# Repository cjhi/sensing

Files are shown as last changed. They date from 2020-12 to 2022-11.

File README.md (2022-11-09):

# Sensing

Repository for all Olin Rocketry hardware and firmware.

The purpose of the avionics system is to determine when to deploy the drogue and main chutes, and to send the signal to do so to the recovery system. The flight computer contains several sensors to help detect apogee, and a microcontroller to read and process the data and send the signal.

The avionics system consists of

- a commercial-off-the-shelf (COTS) flight computer;
- a student-designed flight computer, which includes sensors, microcontroller, GPS, and radio; and
- a student-designed battery management system (BMS).

The COTS computer is a **\_** model. It has its own batteries, sensors, and radio and can trigger the recovery system independently. It is intended as a backup and is required by IREC competition rules (partly so they have a reliable altitude measurement for the competition). The BMS is described on the Power Management subteam page. It can suppy a steady 3.3V current up to about 1000 mA to the student-designed flight computer board.

**The flight computer consists of a Teensy 3.6 microcontroller and various sensors.**

- The [Teensy 3.6](https://www.pjrc.com/teensy/card9a_rev1.pdf) is computationally powerful enough for complex data processing, has many interrupt pins, and many pins in general for connecting multiple sensors. It also has a built-in SD card reader. The decision to use it was made before the Fall 2020 semester; other options were considered and may be viable for future iterations. The main drawback of the Teensy 3.6 is its cost, at around $30. This makes having multiple prototypes very expensive, especially if we want to distribute copies to team members living in separate places.
- We considered 3 different inertial measurement units (IMUs, or accelerometers):
  - [ADXL345](https://www.analog.com/media/en/technical-documentation/data-sheets/ADXL345.pdf) is a very common 3-axis accelerometer. It is widely available and was already in stock from JLC, the company manufacturing our board. This means our boards will have the ADXL345 already populated when it is shipped to us, a bonus.
  - [BMI088](https://download.mikroe.com/documents/datasheets/BMI088_Datasheet.pdf) is a 6-axis accelerometer and gyroscope (axes 4-6 are angular acceleration).
  - [BNO055](https://cdn-shop.adafruit.com/datasheets/BST_BNO055_DS000_12.pdf) is a 9-axis accelerometer, relative, and absolute gyroscope (axes 7-9 are absolute orientation).

We designed our Rev1 PCB to hold all three IMUs, so that we could test all of them at once. However, as of ordering time in January, the BMI088 and BNO055 were out of stock at Digikey and Mouser, so these were never tested.

- [MPL3115A2](https://www.nxp.com/docs/en/data-sheet/MPL3115A2.pdf) is a barometer calibrated to provide altimetry. It is the most important sensor, as it allows us to determine our absolute altitude. Our simplest apogee detection is triggered by a certain number of consecutive decreasing altitude measurements.
- Header pins for the [Adafruit Ultimate GPS Breakout (Version 3)](https://www.adafruit.com/product/746?__hstc), a $40 complete GPS module.
- Header pins for the [RFM9X LoRa Packet Radio Breakout](https://learn.adafruit.com/adafruit-rfm69hcw-and-rfm96-rfm95-rfm98-lora-packet-padio-breakouts/arduino-wiring), the currenty preferred radio (see Communications subteam page).

**Rev 1 Testing Update: Spring 2021**

The sensors on Rev1 (the ADXL345 accelerometer and the MPL3115A2 barometer) work, and the data can be read over I2C. The current data format is a csv file with time since launch, x, y, and z acceleration, pressure, altitude, and temperature. The readings from the accelerometer have very little noise when at rest (the only test performed so far - others to follow soon). The barometer has some issues. First of all, it has an offset of about 1.7 atmospheres. When those 1.7 atm are subtracted out, however, it provides high precision and sensitivity. The altitude readings are off by the same offset, as I believe they are calculated from the barometer reading anyway. The temperature has some 20 degrees F offset and significant drift of 2-5 degrees F over a few minutes. More testing to follow.

I looked at the specs and realized that the ADXL345 and MPL3115A2 together consume less than 3 mA of current at their max. Since the Teensy can output 250 mA through those pins, I don’t see why to use an external power source; we can just use the 3.3V pins on the Teensy.
The tests I have done have been using the 3.3V pin as a power source.

**Tests performed 3/26/2021:**

**Power supply test:** Get an external power supply and give 3.3V to the power inputs. Test the test points and the Teensy’s Vin pin. Test data logging onto SD card. Test sensors connected only to external power supply vs. connected to Teensy 3.3V pin vs. connected to both.

**Results:**
The transistor part of the Rev1 power management circuit did not work. For some reason, there was always only ~0.6V on both the gate and drain pins, and so 0.6V on the rest of the PCB. I tried several pin configurations and nothing helped. It worked fine when I bypassed the transistor and powered 3.3V to both the Teensy and the PCB.
The Teensy could not write to the SD card when the PCB and Teensy were powered independently; it only works when the rest of the PCB is powered through the Teensy’s dedicated 3.3V pin. Therefore, I recommend just using the Teensy’s 3.3V pin to power the sensors.

In this case, I suggest the voltage supplied by the BMS should be 3.6V instead of 3.3V, so that the linear voltage regulator on the Teensy can effectively supply the 3.3V to the sensors. Voltage regulators necessariy have a small voltage drop across them, although I came across a [source](https://forum.pjrc.com/threads/55789-Power-Teensy-3-6-with-lipo-battery?p=203568&viewfull=1#post203568) that says the Teensy will bypass its voltage regulator if the voltage is too low, so there is not necessarily an issue.

**MPL3115A2 Accuracy Test:** Take the Rev1 board up and down the stairs of the MAC building 2 times and measure altitude difference.

**Results:**
The readings are inaccurate, yet very precise. The pressure has reads on the order of 200 kPa, which is double what is expected (1 atmosphere is about 100 kPa), and the temperature reads 90 degrees F in a 70 degree room. Yet after the offset is subtracted, the sensor tracks changes in height of less than 20 feet (the distance between floors in the MAC, and the highest resolution analyzed) quite well. The graph below shows the corrected elevation and temperature over the course of my trip up and down the stairs of the MAC, then outside onto the great lawn and up to the 4th floor of West Hall. There is some drift over time as it sat on my desk after “landing,” on the order of 20 feet over 20 minutes. This is worrying, but it will likely not be a problem during a launch lasting a few minutes.

rev1 full schematic

**Developing the Rev 2 board**

With the ADXL345 and MPL3115A2 sensors confirmed to work, the main objective of the Rev 2 board is to make it fit into the avionics bay. The final board is 80mm tall by 72mm wide and has a mounting hole in each corner. The power supply transistor circuit has been replaced with a power multiplexer, a zener diode was added for overvoltage protection, and the power from the BMS goes directly into the Vin pin on the Teensy; the sensors and other circuitry are powered by the Teensy's 3.3V pin as discussed above. Additionally, 5 debugging LEDs, one power LED, and a [buzzer](https://www.digikey.com/en/products/detail/mallory-sonalert-products-inc/PT-1340P-P10-PQ/4996070) have also been added and are controlled by spare digital pins on the Teensy. A 10uF capacitor was added between the power and ground pins of the radio upon testing by the Communications team.

The board has been ordered from JLC and will arrive within a couple days.

## Guide to creating PCBs

**The process for creating the flight computer PCB has multiple stages:**
  1. Components are selected, including the microcontroller and sensors.
  2. Schematics are created for each sensor individually. This mainly involves copying the circuit diagram from the datasheets for each sensor. Every sensor needs at least two capacitors for its power source, and some require external pull-up resistors, for example. The BNO055 is connected to an external crystal oscillator. It’s also a good idea to add test points (basically large, labelled vias) for debugging purposes. We tried to add a test point to every trace on the schematic that would not be directly connected to the microcontroller (because we can access those traces directly through the microcontroller’s pins). 
  3. For the Rev1 board, footprints for the BNO055 and MPL3115A2 were created by copying the dimensions given by the datasheets. The other footprints were downloaded from snapeda.com. In reality, the only reason to create them manually is to get practice with KiCAD, which is why it was done this way for two of the sensors; in future, snapeda.com likely has all the footprints we will need, without the possibility of human error.*
  4. At this stage, layouts are also created for the supporting circuitry surrounding each sensor individually. These layouts will be manually recreated later, but it is easier to go through a few iterations to find the optimal footprint placements now, before all the layouts are combined on one board.
  5. Now, all of the individual schematics are moved into one place. This can be done in the KiCAD schematic editor (eeschema) by clicking File -> Append Schematic Sheet Content -> then navigate to the schematic to import and click Use Relative Path.
  6. Now all the schematics can be hooked up together; in this case it means connecting each sensor’s communication pins to the Teensy and power and ground to the power supply. A small circuit for regulating the power supply from the BMS, as well as header pins for the BMS and GPS and radio breakout boards are also added to this schematic.
  7. Review the schematics with the flight computer sub-team. Hopefully we have been checking in all along, but now is the last chance to make changes before a lot of work goes into the layout. After this, even small changes to the schematic can be very hard to implement in the layout without starting over.
  8. The layout of all the components for the final PCB is created. You cannot copy and paste the layouts created earlier for individual sensors, but you can follow the prior layouts as a guide. For the Rev1 board, we kept the components in the same relative orientation but did not pack them as closely together, to make debugging and potential fixes easier. During the layout process, it will probably make sense to swap the order of some pins connected to the microcontroller, in order to untangle the traces, or reduce the number of times traces have to cross over. Most pins on the Teensy 3.6 can function in the same way, so switching which pins are connected to which sensor is not a problem. Be careful not to switch the order of SCK and SDA; MISO and MOSI; or RX and TX; these pins are not interchangeable.
  9. It's a good idea to add filled zones on the front and back of the board. Having filled zones helps reduce signal noise and is standard practice. It also means there are fewer traces you have to draw. I usually make my filled zones be ground on both sides of the PCB, with an abundance of vias throughout the board to connect the front and back ground planes. Remember to press 'B' to redraw the zones in KiCAD.
  10. When the layout is done and reviewed, it is sent to JLC, our manufacturer. JLC can populate the PCB with basic components like capacitors, resistors, and even the ADXL345. They did not have any of the other sensors in stock, so we will solder those on campus. We will also solder header pins and large components like the power-regulating MOSFET transistor (which will be discontinued in Rev2).
  11. Next up is writing the firmware to test the sensors and hopefully getting some data!

\* In fact, I did make a very significant error while copying the footprint from the datasheet for both the BNO055 and the MPL3115. I copied the pads as they were shown in the datasheet, which was a bottom-up view. What matters for the layout is the top-down view (think about how the sensor sits on the PCB; you want to design the pads so they sit directly beneath the sensor). When you design the pads using the bottom-up view, you get a mirror image of how they are supposed to be. Moreover, since the footprints are often symmetrical, it can be impossible to tell you’ve made a mistake, until you realize that the pins things are supposed to be connected to are actually on the opposite side of the chip.

### Rev2 images

**Rev2 full schematic**

rev2 full schematic

**Rev2 power supply**

rev1 power supply

**Rev2 layout**

rev1 layout

**Rev2 3D model (front)**

rev1 3D model front

**Rev2 3D model (back)**

rev1 3D model back

### Rev1 images

**Rev1 full schematic**

rev1 full schematic

**Rev1 power supply**

rev1 power supply

**Rev1 layout**

rev1 layout

**Rev1 3D model (front)**

rev1 3D model front

**Rev1 3D model (back)**

rev1 3D model back

## Ordering PCBs From JLCPCB

For ordering the boards, go to JLCPCB.com (https://jlcpcb.com/RAT), and click on "Quote Now" button.

jlcpcb quote

JLCPCB (ShenzhenJLC Electronics Co., Ltd.), is the largest PCB prototype enterprise in China, and a high-tech manufacturer specializing in quick PCB prototype and small-batch PCB production. You can order a minimum of 5 PCBs for just $2.

First: Upload the gerber files for the board by clicking the "Add gerber file" button. You’ll notice a message at the bottom if the file is successfully uploaded.

jlcpbc gerber

A correctly uploaded gerber folder renders the board as follows:

jlcpcb render

Second: In order to get the board assembled (optional, based on the project requirements), select the "SMT Assembly option. It is important to select the side of the PCB that needs to be assembled, as well as the quantity for SMT. Press the "Confirm" button, then press the "Next" button.

jlcpcb smt

Third: upload the BOM (Bill of Material) and CPL (Component Placement List) files and click the "Next" button. It is necessary to make sure that each of these files follow the jlcpcb specified BOM and CPL formats, respectively:

- [Sample BOM](https://jlcpcb.com//video/JLCSMT_Sample_BOM1.xlsx?_ga=2.42560357.1905056644.1612161700-100444678.1610257845)
- [Sample CPL](https://jlcpcb.com//video/JLCSMT_Sample_CPL1.xlsx?_ga=2.42560357.1905056644.1612161700-100444678.1610257845)
- [SMT FAQ's](https://support.jlcpcb.com/category/78-smt-assembly?_ga=2.42560357.1905056644.1612161700-100444678.1610257845)

Note: If there is an issue with the BOM/CPL formatting, the the page will keep erroring out until it is resolved.

jlcpcb bom

Fourth: The parts are automatically detected through the uploaded BOM. They are also matched against jlcpcb's in-stock parts. It is important to go through each row and confirm if the auto-detected parts are the desired parts. Some parts will remain undetected if they cannot be assembled through SMT and require manual assembly post-deilvery.

jlcpcb parts

Fifth: The website renders an assembled board using the CPL file. This feature can be used to review the placement of the components (including orientation). Once carefull reviewed, the next step is to download a list of parts remaining to be assembled towards the bottom of this page view. It is important to place an order for the remaining components to be manually assembled upon delivery.

jlcpcb review

Sixth: Click on the “Save to Cart” button. Then, click on the "Secure Checkout" button.

jlcpcb checkout

Last: Add the payment details and choose the suitable delivery method (this includes FedEx, DHL, and standard mail options). Then, place the order.

Optional: To review the production status of the board, click on the "Order History" button under username. Then, click on In Production > view progress to obtain timestamps for each of the production steps in real time.

jlcpcb production

jlcpcb production progress

**Design Reviews**

-November 11, 2022 6:00 PM

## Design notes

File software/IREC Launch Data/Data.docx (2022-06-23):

0

RSSI: -102

Got: Time: 14091326 Phase: 2 Arm: 1299.062500 Main: 1741.262451 Alt: 1284.187500

RSSI: -102

Got: Time: 140914500

RSSI: -102

Got: Time: 14091326 Phase: 2 Arm: 1299.062500 Main: 1741.262451 Alt: 1284.187500

RSSI: -102

Got: Time: 140914500

RSSI: -102

Got: Time: 14091326 Phase: 2 Arm: 1299.062500 Main: 1741.262451 Alt: 1284.187500

RSSI: -102

Got: Time: 140914Arduino LoRa RX Test!

LoRa radio init OK!

Set Freq to: 915.00

Got: Time: 14093661 Phase: 2 Arm: 1299.062500 Main: 1741.262451 Alt: 1284.312500

RSSI: -103

Got: Time: 14093828 Phase: 2 Arm: 1299.062500 Main: 1741.262451 Alt: 1284.312500

RSSI: -102

Got: Time: 14093994 Phase: 2 Arm: 1299.062500 Main: 1741.262451 Alt: 1284.250000

RSSI: -102

Got: Time: 14094161 Phase: 2 Arm: 1299.062500 Main: 1741.262451 Alt: 1284.125000

RSSI: -102

Got: Time: 14094328 Phase: 2 Arm: 1299.062500 Main: 1741.262451 Alt: 1283.437500

RSSI: -101

Got: Time: 14094495 Phase: 2 Arm: 1299.062500 Main: 1741.262451 Alt: 1284.625000

RSSI: -102

Got: Time: 14094661 Phase: 2 Arm: 1299.062500 Main: 1741.262451 Alt: 1284.312500

RSSI: -103

Got: Time: 14094828 Phase: 2 Arm: 1299.062500 Main: 1741.262451 Alt: 1284.312500

RSSI: -103

Got: Time: 14094995 Phase: 2 Arm: 1299.062500 Main: 1741.262451 Alt: 1284.375000

RSSI: -102

Got: Time: 14095162 Phase: 2 Arm: 1299.062500 Main: 1741.262451 Alt: 1283.937500

RSSI: -99

Got: Time: 14095329 Phase: 2 Arm: 1299.062500 Main: 1741.262451 Alt: 1284.187500

RSSI: -103

Got: Time: 14095495 Phase: 2 Arm: 1299.062500 Main: 1741.262451 Alt: 1284.187500

RSSI: -103

Got: Time: 14095662 Phase: 2 Arm: 1299.062500 Main: 1741.262451 Alt: 1284.437500

RSSI: -103

Got: Time: 14095829 Phase: 2 Arm: 1299.062500 Main: 1741.262451 Alt: 1283.875000

RSSI: -103

Got: Time: 14095996 Phase: 2 Arm: 1299.062500 Main: 1741.262451 Alt: 1284.375000

RSSI: -102

Got: Time: 14096162 Phase: 2 Arm: 1299.062500 Main: 1741.262451 Alt: 1283.937500

RSSI: -101

Got: Time: 14096329 Phase: 2 Arm: 1299.062500 Main: 1741.262451 Alt: 1284.187500

RSSI: -102

Got: Time: 14096496 Phase: 2 Arm: 1299.062500 Main: 1741.262451 Alt: 1283.937500

RSSI: -102

Got: Time: 14096663 Phase: 2 Arm: 1299.062500 Main: 1741.262451 Alt: 1284.000000

RSSI: -103

Got: Time: 14096829 Phase: 2 Arm: 1299.062500 Main: 1741.262451 Alt: 1284.125000

RSSI: -102

Got: Time: 14096996 Phase: 2 Arm: 1299.062500 Main: 1741.262451 Alt: 1284.312500

RSSI: -103

Got: Time: 14097163 Phase: 2 Arm: 1299.062500 Main: 1741.262451 Alt: 1283.812500

RSSI: -99

Got: Time: 14097330 Phase: 2 Arm: 1299.062500 Main: 1741.262451 Alt: 1284.375000

RSSI: -102

Got: Time: 14097497 Phase: 2 Arm: 1299.062500 Main: 1741.262451 Alt: 1283.562500

RSSI: -102

Got: Time: 14097663 Phase: 2 Arm: 1299.062500 Main: 1741.262451 Alt: 1283.937500

RSSI: -103

Got: Time: 14097830 Phase: 2 Arm: 1299.062500 Main: 1741.262451 Alt: 1284.375000

RSSI: -103

Got: Time: 14097997 Phase: 2 Arm: 1299.062500 Main: 1741.262451 Alt: 1284.125000

RSSI: -103

Got: Time: 14098164 Phase: 2 Arm: 1299.062500 Main: 1741.262451 Alt: 1284.312500

RSSI: -98

Got: Time: 14098330 Phase: 2 Arm: 1299.062500 Main: 1741.262451 Alt: 1284.187500

RSSI: -103

Got: Time: 14098497 Phase: 2 Arm: 1299.062500 Main: 1741.262451 Alt: 1284.187500

RSSI: -102

Got: Time: 14098664 Phase: 2 Arm: 1299.062500 Main: 1741.262451 Alt: 1283.937500

RSSI: -103

Got: Time: 14098831 Phase: 2 Arm: 1299.062500 Main: 1741.262451 Alt: 1283.875000

RSSI: -102

Got: Time: 14098997 Phase: 2 Arm: 1299.062500 Main: 1741.262451 Alt: 1283.937500

RSSI: -103

Got: Time: 14099164 Phase: 2 Arm: 1299.062500 Main: 1741.262451 Alt: 1283.312500

RSSI: -100

Got: Time: 14099331 Phase: 2 Arm: 1299.062500 Main: 1741.262451 Alt: 1283.312500

RSSI: -99

Got: Time: 14099498 Phase: 2 Arm: 1299.062500 Main: 1741.262451 Alt: 1283.750000

RSSI: -102

Got: Time: 14099665 Phase: 2 Arm: 1299.062500 Main: 1741.262451 Alt: 1283.562500

RSSI: -102

Got: Time: 14099831 Phase: 2 Arm: 1299.062500 Main: 1741.262451 Alt: 1284.187500

RSSI: -102

Got: Time: 14099998 Phase: 2 Arm: 1299.062500 Main: 1741.262451 Alt: 1283.937500

RSSI: -102

Got: Time: 14100165 Phase: 2 Arm: 1299.062500 Main: 1741.262451 Alt: 1284.000000

RSSI: -102

Got: Time: 14100332 Phase: 2 Arm: 1299.062500 Main: 1741.262451 Alt: 1284.062500

RSSI: -103

Got: Time: 14100498 Phase: 2 Arm: 1299.062500 Main: 1741.262451 Alt: 1284.062500

RSSI: -102

Got: Time: 14100665 Phase: 2 Arm: 1299.062500 Main: 1741.262451 Alt: 1283.937500

RSSI: -103

Got: Time: 14100832 Phase: 2 Arm: 1299.062500 Main: 1741.262451 Alt: 1283.875000

RSSI: -103

Got: Time: 14100999 Phase: 2 Arm: 1299.062500 Main: 1741.262451 Alt: 1283.937500

RSSI: -103

Got: Time: 14101165 Phase: 2 Arm: 1299.062500 Main: 1741.262451 Alt: 1284.375000

RSSI: -101

Got: Time: 14101332 Phase: 2 Arm: 1299.062500 Main: 1741.262451 Alt: 1284.000000

RSSI: -103

Got: Time: 14101499 Phase: 2 Arm: 1299.062500 Main: 1741.262451 Alt: 1284.187500

RSSI: -102

Got: Time: 14101666 Phase: 2 Arm: 1299.062500 Main: 1741.262451 Alt: 1284.062500

RSSI: -102

Got: Time: 14101832 Phase: 2 Arm: 1299.062500 Main: 1741.262451 Alt: 1284.000000

RSSI: -102

Got: Time: 14101999 Phase: 2 Arm: 1299.062500 Main: 1741.262451 Alt: 1284.562500

RSSI: -103

Got: Time: 14102166 Phase: 2 Arm: 1299.062500 Main: 1741.262451 Alt: 1283.937500

RSSI: -99

Got: Time: 14102333 Phase: 2 Arm: 1299.062500 Main: 1741.262451 Alt: 1283.562500

RSSI: -102

Got: Time: 14102500 Phase: 2 Arm: 1299.062500 Main: 1741.262451 Alt: 1283.750000

RSSI: -102

Got: Time: 14102666 Phase: 2 Arm: 1299.062500 Main: 1741.262451 Alt: 1284.062500

RSSI: -102

Got: Time: 14102833 Phase: 2 Arm: 1299.062500 Main: 1741.262451 Alt: 1284.375000

RSSI: -102

Got: Time: 14103000 Phase: 2 Arm: 1299.062500 Main: 1741.262451 Alt: 1283.937500

RSSI: -102

Got: Time: 14103167 Phase: 2 Arm: 1299.062500 Main: 1741.262451 Alt: 1284.375000

RSSI: -100

Got: Time: 14103333 Phase: 2 Arm: 1299.062500 Main: 1741.262451 Alt: 1283.625000

RSSI: -102

Got: Time: 14103500 Phase: 2 Arm: 1299.062500 Main: 1741.262451 Alt: 1283.375000

RSSI: -102

Got: Time: 14103667 Phase: 2 Arm: 1299.062500 Main: 1741.262451 Alt: 1283.750000

RSSI: -102

Got: Time: 14103834 Phase: 2 Arm: 1299.062500 Main: 1741.262451 Alt: 1284.375000

RSSI: -102

Got: Time: 14104000 Phase: 2 Arm: 1299.062500 Main: 1741.262451 Alt: 1283.562500

RSSI: -102

Got: Time: 14104167 Phase: 2 Arm: 1299.062500 Main: 1741.262451 Alt: 1283.875000

RSSI: -100

Got: Time: 14104334 Phase: 2 Arm: 1299.062500 Main: 1741.262451 Alt: 1284.250000

RSSI: -100

Got: Time: 14104501 Phase: 2 Arm: 1299.062500 Main: 1741.262451 Alt: 1284.187500

RSSI: -102

Got: Time: 14104668 Phase: 2 Arm: 1299.062500 Main: 1741.262451 Alt: 1284.187500

RSSI: -103

Got: Time: 14104834 Phase: 2 Arm: 1299.062500 Main: 1741.262451 Alt: 1284.562500

RSSI: -102

Got: Time: 14105001 Phase: 2 Arm: 1299.062500 Main: 1741.262451 Alt: 1283.812500

RSSI: -102

Got: Time: 14105168 Phase: 2 Arm: 1299.062500 Main: 1741.262451 Alt: 1284.375000

RSSI: -96

Got: Time: 14105335 Phase: 2 Arm: 1299.062500 Main: 1741.262451 Alt: 1283.937500

RSSI: -102

Got: Time: 14105501 Phase: 2 Arm: 1299.062500 Main: 1741.262451 Alt: 1284.312500

RSSI: -102

Got: Time: 14105668 Phase: 2 Arm: 1299.062500 Main: 1741.262451 Alt: 1283.937500

RSSI: -102

Got: Time: 14105835 Phase: 2 Arm: 1299.062500 Main: 1741.262451 Alt: 1284.000000

RSSI: -102

Got: Time: 14106002 Phase: 2 Arm: 1299.062500 Main: 1741.262451 Alt: 1284.562500

RSSI: -102

Got: Time: 14106168 Phase: 2 Arm: 1299.062500 Main: 1741.262451 Alt: 1283.687500

RSSI: -98

Got: Time: 14106335 Phase: 2 Arm: 1299.062500 Main: 1741.262451 Alt: 1284.187500

RSSI: -102

Got: Time: 14106502 Phase: 2 Arm: 1299.062500 Main: 1741.262451 Alt: 1283.750000

RSSI: -102

Got: Time: 14106669 Phase: 2 Arm: 1299.062500 Main: 1741.262451 Alt: 1283.937500

RSSI: -103

Got: Time: 14106836 Phase: 2 Arm: 1299.062500 Main: 1741.262451 Alt: 1284.375000

RSSI: -103

Got: Time: 14107002 Phase: 2 Arm: 1299.062500 Main: 1741.262451 Alt: 1283.937500

RSSI: -102

Got: Time: 14107169 Phase: 2 Arm: 1299.062500 Main: 1741.262451 Alt: 1283.750000

RSSI: -97

Got: Time: 14107336 Phase: 2 Arm: 1299.062500 Main: 1741.262451 Alt: 1284.062500

RSSI: -102

Got: Time: 14107503 Phase: 2 Arm: 1299.062500 Main: 1741.262451 Alt: 1284.375000

RSSI: -102

Got: Time: 14107669 Phase: 2 Arm: 1299.062500 Main: 1741.262451 Alt: 1283.562500

RSSI: -102

Got: Time: 14107836 Phase: 2 Arm: 1299.062500 Main: 1741.262451 Alt: 1284.250000

RSSI: -103

Got: Time: 14108170 Phase: 2 Arm: 1299.062500 Main: 1741.262451 Alt: 1283.937500

RSSI: -101

Got: Time: 14108336 Phase: 2 Arm: 1299.062500 Main: 1741.262451 Alt: 1283.937500

RSSI: -102

Got: Time: 14108503 Phase: 2 Arm: 1299.062500 Main: 1741.262451 Alt: 1284.500000

RSSI: -102

Got: Time: 14108670 Phase: 2 Arm: 1299.062500 Main: 1741.262451 Alt: 1283.687500

RSSI: -102

Got: Time: 14108837 Phase: 2 Arm: 1299.062500 Main: 1741.262451 Alt: 1284.125000

RSSI: -102

Got: Time: 14109004 Phase: 2 Arm: 1299.062500 Main: 1741.262451 Alt: 1284.000000

RSSI: -102

Got: Time: 14109170 Phase: 2 Arm: 1299.062500 Main: 1741.262451 Alt: 1283.937500

RSSI: -101

Got: Time: 14109337 Phase: 2 Arm: 1299.062500 Main: 1741.262451 Alt: 1284.500000

RSSI: -102

Got: Time: 14109504 Phase: 2 Arm: 1299.062500 Main: 1741.262451 Alt: 1284.187500

RSSI: -102

Got: Time: 14109671 Phase: 2 Arm: 1299.062500 Main: 1741.262451 Alt: 1284.562500

RSSI: -102

Got: Time: 14109837 Phase: 2 Arm: 1299.062500 Main: 1741.262451 Alt: 1284.125000

RSSI: -102

Got: Time: 14110004 Phase: 2 Arm: 1299.062500 Main: 1741.262451 Alt: 1284.375000

RSSI: -103

Got: Time: 14110171 Phase: 2 Arm: 1299.062500 Main: 1741.262451 Alt: 1284.500000

RSSI: -101

Got: Time: 14110338 Phase: 2 Arm: 1299.062500 Main: 1741.262451 Alt: 1284.312500

RSSI: -102

Got: Time: 14110504 Phase: 2 Arm: 1299.062500 Main: 1741.262451 Alt: 1284.187500

RSSI: -102

Got: Time: 14110671 Phase: 2 Arm: 1299.062500 Main: 1741.262451 Alt: 1283.750000

RSSI: -102

Got: Time: 14110838 Phase: 2 Arm: 1299.062500 Main: 1741.262451 Alt: 1283.687500

RSSI: -102

Got: Time: 14111005 Phase: 2 Arm: 1299.062500 Main: 1741.262451 Alt: 1283.562500

RSSI: -102

Got: Time: 14111172 Phase: 2 Arm: 1299.062500 Main: 1741.262451 Alt: 1283.750000

RSSI: -102

Got: Time: 14111338 Phase: 2 Arm: 1299.062500 Main: 1741.262451 Alt: 1284.687500

RSSI: -102

Got: Time: 14111505 Phase: 2 Arm: 1299.062500 Main: 1741.262451 Alt: 1283.750000

RSSI: -102

Got: Time: 14111672 Phase: 2 Arm: 1299.062500 Main: 1741.262451 Alt: 1284.062500

RSSI: -102

Got: Time: 14111839 Phase: 2 Arm: 1299.062500 Main: 1741.262451 Alt: 1283.812500

RSSI: -102

Got: Time: 14112005 Phase: 2 Arm: 1299.062500 Main: 1741.262451 Alt: 1284.187500

RSSI: -102

Got: Time: 14112172 Phase: 2 Arm: 1299.062500 Main: 1741.262451 Alt: 1284.750000

RSSI: -101

Got: Time: 14112339 Phase: 2 Arm: 1299.062500 Main: 1741.262451 Alt: 1284.187500

RSSI: -102

Got: Time: 14112506 Phase: 2 Arm: 1299.062500 Main: 1741.262451 Alt: 1284.187500

RSSI: -102

Got: Time: 14112672 Phase: 2 Arm: 1299.062500 Main: 1741.262451 Alt: 1283.750000

RSSI: -102

Got: Time: 14112839 Phase: 2 Arm: 1299.062500 Main: 1741.262451 Alt: 1284.187500

RSSI: -102

Got: Time: 14113006 Phase: 2 Arm: 1299.062500 Main: 1741.262451 Alt: 1284.562500

RSSI: -102

Got: Time: 14113173 Phase: 2 Arm: 1299.062500 Main: 1741.262451 Alt: 1284.125000

RSSI: -100

Got: Time: 14113339 Phase: 2 Arm: 1299.062500 Main: 1741.262451 Alt: 1283.937500

RSSI: -102

Got: Time: 14113506 Phase: 2 Arm: 1299.062500 Main: 1741.262451 Alt: 1283.937500

RSSI: -102

Got: Time: 14113673 Phase: 2 Arm: 1299.062500 Main: 1741.262451 Alt: 1283.750000

RSSI: -102

Got: Time: 14113840 Phase: 2 Arm: 1299.062500 Main: 1741.262451 Alt: 1284.187500

RSSI: -102

Got: Time: 14114007 Phase: 2 Arm: 1299.062500 Main: 1741.262451 Alt: 1283.250000

RSSI: -102

Got: Time: 14114173 Phase: 2 Arm: 1299.062500 Main: 1741.262451 Alt: 1284.562500

RSSI: -101

Got: Time: 14114340 Phase: 2 Arm: 1299.062500 Main: 1741.262451 Alt: 1284.437500

RSSI: -101

Got: Time: 14114507 Phase: 2 Arm: 1299.062500 Main: 1741.262451 Alt: 1283.750000

RSSI: -102

Got: Time: 14114674 Phase: 2 Arm: 1299.062500 Main: 1741.262451 Alt: 1284.750000

RSSI: -102

Got: Time: 14114840 Phase: 2 Arm: 1299.062500 Main: 1741.262451 Alt: 1284.250000

RSSI: -102

Got: Time: 14115007 Phase: 2 Arm: 1299.062500 Main: 1741.262451 Alt: 1284.250000

RSSI: -102

Got: Time: 14115174 Phase: 2 Arm: 1299.062500 Main: 1741.262451 Alt: 1283.687500

RSSI: -98

Got: Time: 14115341 Phase: 2 Arm: 1299.062500 Main: 1741.262451 Alt: 1284.062500

RSSI: -102

Got: Time: 14115507 Phase: 2 Arm: 1299.062500 Main: 1741.262451 Alt: 1284.375000

RSSI: -102

Got: Time: 14115674 Phase: 2 Arm: 1299.062500 Main: 1741.262451 Alt: 1284.187500

RSSI: -102

Got: Time: 14115841 Phase: 2 Arm: 1299.062500 Main: 1741.262451 Alt: 1284.687500

RSSI: -102

Got: Time: 14116008 Phase: 2 Arm: 1299.062500 Main: 1741.262451 Alt: 1284.375000

RSSI: -102

Got: Time: 14116175 Phase: 2 Arm: 1299.062500 Main: 1741.262451 Alt: 1284.187500

RSSI: -97

Got: Time: 14116341 Phase: 2 Arm: 1299.062500 Main: 1741.262451 Alt: 1284.000000

RSSI: -102

Got: Time: 14116508 Phase: 2 Arm: 1299.062500 Main: 1741.262451 Alt: 1284.812500

RSSI: -102

Got: Time: 14116675 Phase: 2 Arm: 1299.062500 Main: 1741.262451 Alt: 1284.250000

RSSI: -102

Got: Time: 14116842 Phase: 2 Arm: 1299.062500 Main: 1741.262451 Alt: 1284.500000

RSSI: -103

Got: Time: 14117008 Phase: 2 Arm: 1299.062500 Main: 1741.262451 Alt: 1284.375000

RSSI: -102

Got: Time: 14117175 Phase: 2 Arm: 1299.062500 Main: 1741.262451 Alt: 1283.937500

RSSI: -98

Got: Time: 14117342 Phase: 2 Arm: 1299.062500 Main: 1741.262451 Alt: 1283.812500

RSSI: -102

Got: Time: 14117509 Phase: 2 Arm: 1299.062500 Main: 1741.262451 Alt: 1284.125000

RSSI: -102

Got: Time: 14117675 Phase: 2 Arm: 1299.062500 Main: 1741.262451 Alt: 1284.187500

RSSI: -102

Got: Time: 14117842 Phase: 2 Arm: 1299.062500 Main: 1741.262451 Alt: 1284.375000

RSSI: -102

Got: Time: 14118009 Phase: 2 Arm: 1299.062500 Main: 1741.262451 Alt: 1284.000000

RSSI: -102

Got: Time: 14118176 Phase: 2 Arm: 1299.062500 Main: 1741.262451 Alt: 1283.937500

RSSI: -97

Got: Time: 14118343 Phase: 2 Arm: 1299.062500 Main: 1741.262451 Alt: 1283.750000

RSSI: -102

Got: Time: 14118509 Phase: 2 Arm: 1299.062500 Main: 1741.262451 Alt: 1283.750000

RSSI: -102

Got: Time: 14118676 Phase: 2 Arm: 1299.062500 Main: 1741.262451 Alt: 1284.562500

RSSI: -102

Got: Time: 14118843 Phase: 2 Arm: 1299.062500 Main: 1741.262451 Alt: 1284.125000

RSSI: -102

Got: Time: 14119010 Phase: 2 Arm: 1299.062500 Main: 1741.262451 Alt: 1284.437500

RSSI: -102

Got: Time: 14119176 Phase: 2 Arm: 1299.062500 Main: 1741.262451 Alt: 1284.312500

RSSI: -98

Got: Time: 14119343 Phase: 2 Arm: 1299.062500 Main: 1741.262451 Alt: 1283.937500

RSSI: -100

Got: Time: 14119510 Phase: 2 Arm: 1299.062500 Main: 1741.262451 Alt: 1283.687500

RSSI: -103

Got: Time: 14119677 Phase: 2 Arm: 1299.062500 Main: 1741.262451 Alt: 1284.187500

RSSI: -103

Got: Time: 14119843 Phase: 2 Arm: 1299.062500 Main: 1741.262451 Alt: 1284.375000

RSSI: -103

Got: Time: 14120177 Phase: 2 Arm: 1299.062500 Main: 1741.262451 Alt: 1284.312500

RSSI: -99

Got: Time: 14120344 Phase: 2 Arm: 1299.062500 Main: 1741.262451 Alt: 1284.562500

RSSI: -103

Got: Time: 14120510 Phase: 2 Arm: 1299.062500 Main: 1741.262451 Alt: 1284.937500

RSSI: -103

Got: Time: 14120677 Phase: 2 Arm: 1299.062500 Main: 1741.262451 Alt: 1284.312500

RSSI: -103

Got: Time: 14120844 Phase: 2 Arm: 1299.062500 Main: 1741.262451 Alt: 1284.562500

RSSI: -103

Got: Time: 14121011 Phase: 2 Arm: 1299.062500 Main: 1741.262451 Alt: 1284.437500

RSSI: -102

Got: Time: 14121178 Phase: 2 Arm: 1299.062500 Main: 1741.262451 Alt: 1284.687500

RSSI: -99

Got: Time: 14121344 Phase: 2 Arm: 1299.062500 Main: 1741.262451 Alt: 1284.562500

RSSI: -103

Got: Time: 14121511 Phase: 2 Arm: 1299.062500 Main: 1741.262451 Alt: 1284.375000

RSSI: -103

Got: Time: 14121678 Phase: 2 Arm: 1299.062500 Main: 1741.262451 Alt: 1284.375000

RSSI: -103

Got: Time: 14121845 Phase: 2 Arm: 1299.062500 Main: 1741.262451 Alt: 1283.937500

RSSI: -102

Got: Time: 14122011 Phase: 2 Arm: 1299.062500 Main: 1741.262451 Alt: 1284.375000

RSSI: -103

Got: Time: 14122178 Phase: 2 Arm: 1299.062500 Main: 1741.262451 Alt: 1284.125000

RSSI: -100

Got: Time: 14122345 Phase: 2 Arm: 1299.062500 Main: 1741.262451 Alt: 1283.875000

RSSI: -103

Got: Time: 14122512 Phase: 2 Arm: 1299.062500 Main: 1741.262451 Alt: 1284.375000

RSSI: -103

Got: Time: 14122678 Phase: 2 Arm: 1299.062500 Main: 1741.262451 Alt: 1284.000000

RSSI: -102

Got: Time: 14122845 Phase: 2 Arm: 1299.062500 Main: 1741.262451 Alt: 1283.812500

RSSI: -103

Got: Time: 14123012 Phase: 2 Arm: 1299.062500 Main: 1741.262451 Alt: 1284.250000

RSSI: -103

Got: Time: 14123179 Phase: 2 Arm: 1299.062500 Main: 1741.262451 Alt: 1284.062500

RSSI: -99

Got: Time: 14123346 Phase: 2 Arm: 1299.062500 Main: 1741.262451 Alt: 1283.875000

RSSI: -102

Got: Time: 14123512 Phase: 2 Arm: 1299.062500 Main: 1741.262451 Alt: 1283.937500

RSSI: -103

Got: Time: 14123679 Phase: 2 Arm: 1299.062500 Main: 1741.262451 Alt: 1283.625000

RSSI: -102

Got: Time: 14123846 Phase: 2 Arm: 1299.062500 Main: 1741.262451 Alt: 1284.187500

RSSI: -103

Got: Time: 14124013 Phase: 2 Arm: 1299.062500 Main: 1741.262451 Alt: 1284.562500

RSSI: -102

Got: Time: 14124179 Phase: 2 Arm: 1299.062500 Main: 1741.262451 Alt: 1284.187500

RSSI: -100

Got: Time: 14124346 Phase: 2 Arm: 1299.062500 Main: 1741.262451 Alt: 1283.937500

RSSI: -99

Got: Time: 14124513 Phase: 2 Arm: 1299.062500 Main: 1741.262451 Alt: 1284.375000

RSSI: -102

Got: Time: 14124680 Phase: 2 Arm: 1299.062500 Main: 1741.262451 Alt: 1284.187500

RSSI: -102

Got: Time: 14124846 Phase: 2 Arm: 1299.062500 Main: 1741.262451 Alt: 1284.062500

RSSI: -102

Got: Time: 14125013 Phase: 2 Arm: 1299.062500 Main: 1741.262451 Alt: 1284.187500

RSSI: -102

Got: Time: 14125180 Phase: 2 Arm: 1299.062500 Main: 1741.262451 Alt: 1284.250000

RSSI: -98

Got: Time: 14125347 Phase: 2 Arm: 1299.062500 Main: 1741.262451 Alt: 1284.187500

RSSI: -102

Got: Time: 14125514 Phase: 2 Arm: 1299.062500 Main: 1741.262451 Alt: 1284.375000

RSSI: -102

Got: Time: 14125680 Phase: 2 Arm: 1299.062500 Main: 1741.262451 Alt: 1283.937500

RSSI: -102

Got: Time: 14125847 Phase: 2 Arm: 1299.062500 Main: 1741.262451 Alt: 1284.437500

RSSI: -103

Got: Time: 14126014 Phase: 2 Arm: 1299.062500 Main: 1741.262451 Alt: 1284.187500

RSSI: -103

Got: Time: 14126181 Phase: 2 Arm: 1299.062500 Main: 1741.262451 Alt: 1284.250000

RSSI: -101

Got: Time: 14126347 Phase: 2 Arm: 1299.062500 Main: 1741.262451 Alt: 1283.875000

RSSI: -102

Got: Time: 14126514 Phase: 2 Arm: 1299.062500 Main: 1741.262451 Alt: 1284.375000

RSSI: -103

Got: Time: 14126681 Phase: 2 Arm: 1299.062500 Main: 1741.262451 Alt: 1284.187500

RSSI: -102

Got: Time: 14126848 Phase: 2 Arm: 1299.062500 Main: 1741.262451 Alt: 1283.500000

RSSI: -103

Got: Time: 14127014 Phase: 2 Arm: 1299.062500 Main: 1741.262451 Alt: 1284.375000

RSSI: -103

Got: Time: 14127181 Phase: 2 Arm: 1299.062500 Main: 1741.262451 Alt: 1283.937500

RSSI: -100

Got: Time: 14127348 Phase: 2 Arm: 1299.062500 Main: 1741.262451 Alt: 1283.750000

RSSI: -103

Got: Time: 14127515 Phase: 2 Arm: 1299.062500 Main: 1741.262451 Alt: 1284.312500

RSSI: -103

Got: Time: 14127682 Phase: 2 Arm: 1299.062500 Main: 1741.262451 Alt: 1284.000000

RSSI: -103

Got: Time: 14127848 Phase: 2 Arm: 1299.062500 Main: 1741.262451 Alt: 1284.312500

RSSI: -103

Got: Time: 14128015 Phase: 2 Arm: 1299.062500 Main: 1741.262451 Alt: 1283.812500

RSSI: -103

Got: Time: 14128182 Phase: 2 Arm: 1299.062500 Main: 1741.262451 Alt: 1284.187500

RSSI: -101

Got: Time: 14128349 Phase: 2 Arm: 1299.062500 Main: 1741.262451 Alt: 1283.875000

RSSI: -102

Got: Time: 14128515 Phase: 2 Arm: 1299.062500 Main: 1741.262451 Alt: 1284.625000

RSSI: -102

Got: Time: 14128682 Phase: 2 Arm: 1299.062500 Main: 1741.262451 Alt: 1283.937500

RSSI: -103

Got: Time: 14128849 Phase: 2 Arm: 1299.062500 Main: 1741.262451 Alt: 1284.375000

RSSI: -103

Got: Time: 14129016 Phase: 2 Arm: 1299.062500 Main: 1741.262451 Alt: 1284.500000

RSSI: -102

Got: Time: 14129182 Phase: 2 Arm: 1299.062500 Main: 1741.262451 Alt: 1284.187500

RSSI: -98

Got: Time: 14129349 Phase: 2 Arm: 1299.062500 Main: 1741.262451 Alt: 1284.250000

RSSI: -100

Got: Time: 14129516 Phase: 2 Arm: 1299.062500 Main: 1741.262451 Alt: 1284.250000

RSSI: -102

Got: Time: 14129683 Phase: 2 Arm: 1299.062500 Main: 1741.262451 Alt: 1284.250000

RSSI: -103

Got: Time: 14129849 Phase: 2 Arm: 1299.062500 Main: 1741.262451 Alt: 1284.562500

RSSI: -103

Got: Time: 14130016 Phase: 2 Arm: 1299.062500 Main: 1741.262451 Alt: 1284.375000

RSSI: -103

Got: Time: 14130183 Phase: 2 Arm: 1299.062500 Main: 1741.262451 Alt: 1283.812500

RSSI: -99

Got: Time: 14130350 Phase: 2 Arm: 1299.062500 Main: 1741.262451 Alt: 1284.437500

RSSI: -102

Got: Time: 14130517 Phase: 2 Arm: 1299.062500 Main: 1741.262451 Alt: 1285.000000

RSSI: -102

Got: Time: 14130683 Phase: 2 Arm: 1299.062500 Main: 1741.262451 Alt: 1284.437500

RSSI: -102

Got: Time: 14130850 Phase: 2 Arm: 1299.062500 Main: 1741.262451 Alt: 1284.375000

RSSI: -102

Got: Time: 14131017 Phase: 2 Arm: 1299.062500 Main: 1741.262451 Alt: 1283.937500

RSSI: -102

Got: Time: 14131184 Phase: 2 Arm: 1299.062500 Main: 1741.262451 Alt: 1284.500000

RSSI: -98

Got: Time: 14131350 Phase: 2 Arm: 1299.062500 Main: 1741.262451 Alt: 1283.562500

RSSI: -103

Got: Time: 14131517 Phase: 2 Arm: 1299.062500 Main: 1741.262451 Alt: 1284.750000

RSSI: -103

Got: Time: 14131684 Phase: 2 Arm: 1299.062500 Main: 1741.262451 Alt: 1284.062500

RSSI: -102

Got: Time: 14131851 Phase: 2 Arm: 1299.062500 Main: 1741.262451 Alt: 1283.812500

RSSI: -103

Got: Time: 14132017 Phase: 2 Arm: 1299.062500 Main: 1741.262451 Alt: 1284.375000

RSSI: -103

Got: Time: 14132184 Phase: 2 Arm: 1299.062500 Main: 1741.262451 Alt: 1283.125000

RSSI: -100

Got: Time: 14132351 Phase: 2 Arm: 1299.062500 Main: 1741.262451 Alt: 1283.562500

RSSI: -103

Got: Time: 14132518 Phase: 2 Arm: 1299.062500 Main: 1741.262451 Alt: 1284.000000

RSSI: -102

Got: Time: 14132685 Phase: 2 Arm: 1299.062500 Main: 1741.262451 Alt: 1284.187500

RSSI: -102

Got: Time: 14132851 Phase: 2 Arm: 1299.062500 Main: 1741.262451 Alt: 1283.562500

RSSI: -103

Got: Time: 14133018 Phase: 2 Arm: 1299.062500 Main: 1741.262451 Alt: 1283.937500

RSSI: -103

Got: Time: 14133185 Phase: 2 Arm: 1299.062500 Main: 1741.262451 Alt: 1284.312500

RSSI: -99

Got: Time: 14133352 Phase: 2 Arm: 1299.062500 Main: 1741.262451 Alt: 1283.625000

RSSI: -102

Got: Time: 14133518 Phase: 2 Arm: 1299.062500 Main: 1741.262451 Alt: 1284.562500

RSSI: -102

Got: Time: 14133685 Phase: 2 Arm: 1299.062500 Main: 1741.262451 Alt: 1284.062500

RSSI: -102

Got: Time: 14133852 Phase: 2 Arm: 1299.062500 Main: 1741.262451 Alt: 1284.375000

RSSI: -103

Got: Time: 14134019 Phase: 2 Arm: 1299.062500 Main: 1741.262451 Alt: 1283.875000

RSSI: -103

Got: Time: 14134185 Phase: 2 Arm: 1299.062500 Main: 1741.262451 Alt: 1284.375000

RSSI: -102

Got: Time: 14134352 Phase: 2 Arm: 1299.062500 Main: 1741.262451 Alt: 1283.937500

RSSI: -97

Got: Time: 14134519 Phase: 2 Arm: 1299.062500 Main: 1741.262451 Alt: 1283.812500

RSSI: -103

Got: Time: 14134686 Phase: 2 Arm: 1299.062500 Main: 1741.262451 Alt: 1284.625000

RSSI: -103

Got: Time: 14134853 Phase: 2 Arm: 1299.062500 Main: 1741.262451 Alt: 1284.312500

RSSI: -103

Got: Time: 14135019 Phase: 2 Arm: 1299.062500 Main: 1741.262451 Alt: 1284.312500

RSSI: -101

Got: Time: 14135186 Phase: 2 Arm: 1299.062500 Main: 1741.262451 Alt: 1284.562500

RSSI: -100

Got: Time: 14135353 Phase: 2 Arm: 1299.062500 Main: 1741.262451 Alt: 1283.937500

RSSI: -104

Got: Time: 14135520 Phase: 2 Arm: 1299.062500 Main: 1741.262451 Alt: 1284.250000

RSSI: -104

Got: Time: 14135686 Phase: 2 Arm: 1299.062500 Main: 1741.262451 Alt: 1284.187500

RSSI: -104

Got: Time: 14135853 Phase: 2 Arm: 1299.062500 Main: 1741.262451 Alt: 1284.000000

RSSI: -104

Got: Time: 14136020 Phase: 2 Arm: 1299.062500 Main: 1741.262451 Alt: 1283.937500

RSSI: -102

Got: Time: 14136187 Phase: 2 Arm: 1299.062500 Main: 1741.262451 Alt: 1284.562500

RSSI: -101

Got: Time: 14136353 Phase: 2 Arm: 1299.062500 Main: 1741.262451 Alt: 1283.125000

RSSI: -105

Got: Time: 14136520 Phase: 2 Arm: 1299.062500 Main: 1741.262451 Alt: 1284.062500

RSSI: -105

Got: Time: 14136687 Phase: 2 Arm: 1299.062500 Main: 1741.262451 Alt: 1284.375000

RSSI: -104

Got: Time: 14136854 Phase: 2 Arm: 1299.062500 Main: 1741.262451 Alt: 1283.937500

RSSI: -104

Got: Time: 14137020 Phase: 2 Arm: 1299.062500 Main: 1741.262451 Alt: 1284.062500

RSSI: -102

Got: Time: 14137187 Phase: 2 Arm: 1299.062500 Main: 1741.262451 Alt: 1284.375000

RSSI: -101

Got: Time: 14137354 Phase: 2 Arm: 1299.062500 Main: 1741.262451 Alt: 1284.062500

RSSI: -104

Got: Time: 14137521 Phase: 2 Arm: 1299.062500 Main: 1741.262451 Alt: 1284.500000

RSSI: -104

Got: Time: 14137688 Phase: 2 Arm: 1299.062500 Main: 1741.262451 Alt: 1284.250000

RSSI: -103

Got: Time: 14137854 Phase: 2 Arm: 1299.062500 Main: 1741.262451 Alt: 1284.125000

RSSI: -103

Got: Time: 14138021 Phase: 2 Arm: 1299.062500 Main: 1741.262451 Alt: 1284.062500

RSSI: -101

Got: Time: 14138188 Phase: 2 Arm: 1299.062500 Main: 1741.262451 Alt: 1284.187500

RSSI: -99

Got: Time: 14138355 Phase: 2 Arm: 1299.062500 Main: 1741.262451 Alt: 1283.937500

RSSI: -102

Got: Time: 14138521 Phase: 2 Arm: 1299.062500 Main: 1741.262451 Alt: 1284.062500

RSSI: -102

Got: Time: 14138688 Phase: 2 Arm: 1299.062500 Main: 1741.262451 Alt: 1283.750000

RSSI: -103

Got: Time: 14138855 Phase: 2 Arm: 1299.062500 Main: 1741.262451 Alt: 1284.375000

RSSI: -103

Got: Time: 14139022 Phase: 2 Arm: 1299.062500 Main: 1741.262451 Alt: 1283.937500

RSSI: -100

Got: Time: 14139188 Phase: 2 Arm: 1299.062500 Main: 1741.262451 Alt: 1284.062500

RSSI: -102

Got: Time: 14139355 Phase: 2 Arm: 1299.062500 Main: 1741.262451 Alt: 1283.750000

RSSI: -99

Got: Time: 14139522 Phase: 2 Arm: 1299.062500 Main: 1741.262451 Alt: 1284.250000

RSSI: -102

Got: Time: 14139689 Phase: 2 Arm: 1299.062500 Main: 1741.262451 Alt: 1284.687500

RSSI: -102

Got: Time: 14139856 Phase: 2 Arm: 1299.062500 Main: 1741.262451 Alt: 1284.250000

RSSI: -103

Got: Time: 14140022 Phase: 2 Arm: 1299.062500 Main: 1741.262451 Alt: 1284.187500

RSSI: -100

Got: Time: 14140189 Phase: 2 Arm: 1299.062500 Main: 1741.262451 Alt: 1284.187500

RSSI: -100

Got: Time: 14140356 Phase: 2 Arm: 1299.062500 Main: 1741.262451 Alt: 1283.625000

RSSI: -104

Got: Time: 14140523 Phase: 2 Arm: 1299.062500 Main: 1741.262451 Alt: 1284.000000

RSSI: -104

Got: Time: 14140689 Phase: 2 Arm: 1299.062500 Main: 1741.262451 Alt: 1283.937500

RSSI: -105

Got: Time: 14140856 Phase: 2 Arm: 1299.062500 Main: 1741.262451 Alt: 1283.937500

RSSI: -105

Got: Time: 14141023 Phase: 2 Arm: 1299.062500 Main: 1741.262451 Alt: 1284.312500

RSSI: -102

Got: Time: 14141190 Phase: 2 Arm: 1299.062500 Main: 1741.262451 Alt: 1283.812500

RSSI: -102

Got: Time: 14141356 Phase: 2 Arm: 1299.062500 Main: 1741.262451 Alt: 1284.062500

RSSI: -104

Got: Time: 14141523 Phase: 2 Arm: 1299.062500 Main: 1741.262451 Alt: 1284.312500

RSSI: -104

Got: Time: 14141690 Phase: 2 Arm: 1299.062500 Main: 1741.262451 Alt: 1284.187500

RSSI: -105

Got: Time: 14141857 Phase: 2 Arm: 1299.062500 Main: 1741.262451 Alt: 1284.625000

RSSI: -104

Got: Time: 14142024 Phase: 2 Arm: 1299.062500 Main: 1741.262451 Alt: 1283.750000

RSSI: -102

Got: Time: 14142190 Phase: 2 Arm: 1299.062500 Main: 1741.262451 Alt: 1284.375000

RSSI: -100

Got: Time: 14142357 Phase: 2 Arm: 1299.062500 Main: 1741.262451 Alt: 1284.500000

RSSI: -104

Got: Time: 14142524 Phase: 2 Arm: 1299.062500 Main: 1741.262451 Alt: 1284.500000

RSSI: -104

Got: Time: 14142691 Phase: 2 Arm: 1299.062500 Main: 1741.262451 Alt: 1284.125000

RSSI: -104

Got: Time: 14142857 Phase: 2 Arm: 1299.062500 Main: 1741.262451 Alt: 1283.937500

RSSI: -104

Got: Time: 14143024 Phase: 2 Arm: 1299.062500 Main: 1741.262451 Alt: 1284.125000

RSSI: -101

Got: Time: 14143191 Phase: 2 Arm: 1299.062500 Main: 1741.262451 Alt: 1283.562500

RSSI: -100

Got: Time: 14143358 Phase: 2 Arm: 1299.062500 Main: 1741.262451 Alt: 1284.250000

RSSI: -104

Got: Time: 14143524 Phase: 2 Arm: 1299.062500 Main: 1741.262451 Alt: 1284.375000

RSSI: -104

Got: Time: 14143691 Phase: 2 Arm: 1299.062500 Main: 1741.262451 Alt: 1284.187500

RSSI: -105

Got: Time: 14143858 Phase: 2 Arm: 1299.062500 Main: 1741.262451 Alt: 1284.125000

RSSI: -105

Got: Time: 14144025 Phase: 2 Arm: 1299.062500 Main: 1741.262451 Alt: 1284.187500

RSSI: -101

Got: Time: 14144191 Phase: 2 Arm: 1299.062500 Main: 1741.262451 Alt: 1284.250000

RSSI: -99

Got: Time: 14144358 Phase: 2 Arm: 1299.062500 Main: 1741.262451 Alt: 1284.437500

RSSI: -99

Got: Time: 14144525 Phase: 2 Arm: 1299.062500 Main: 1741.262451 Alt: 1284.500000

RSSI: -104

Got: Time: 14144692 Phase: 2 Arm: 1299.062500 Main: 1741.262451 Alt: 1283.750000

RSSI: -104

Got: Time: 14144859 Phase: 2 Arm: 1299.062500 Main: 1741.262451 Alt: 1284.250000

RSSI: -104

Got: Time: 14145025 Phase: 2 Arm: 1299.062500 Main: 1741.262451 Alt: 1284.187500

RSSI: -100

Got: Time: 14145192 Phase: 2 Arm: 1299.062500 Main: 1741.262451 Alt: 1284.437500

RSSI: -100

Got: Time: 14145359 Phase: 2 Arm: 1299.062500 Main: 1741.262451 Alt: 1284.062500

RSSI: -104

Got: Time: 14145526 Phase: 2 Arm: 1299.062500 Main: 1741.262451 Alt: 1283.937500

RSSI: -104

Got: Time: 14145692 Phase: 2 Arm: 1299.062500 Main: 1741.262451 Alt: 1284.437500

RSSI: -105

Got: Time: 14145859 Phase: 2 Arm: 1299.062500 Main: 1741.262451 Alt: 1284.312500

RSSI: -104

Got: Time: 14146026 Phase: 2 Arm: 1299.062500 Main: 1741.262451 Alt: 1284.562500

RSSI: -101

Got: Time: 14146193 Phase: 2 Arm: 1299.062500 Main: 1741.262451 Alt: 1284.250000

RSSI: -100

Got: Time: 14146359 Phase: 2 Arm: 1299.062500 Main: 1741.262451 Alt: 1283.812500

RSSI: -104

Got: Time: 14146526 Phase: 2 Arm: 1299.062500 Main: 1741.262451 Alt: 1284.437500

RSSI: -104

Got: Time: 14146693 Phase: 2 Arm: 1299.062500 Main: 1741.262451 Alt: 1283.750000

RSSI: -104

Got: Time: 14146860 Phase: 2 Arm: 1299.062500 Main: 1741.262451 Alt: 1284.562500

RSSI: -104

Got: Time: 14147027 Phase: 2 Arm: 1299.062500 Main: 1741.262451 Alt: 1283.937500

RSSI: -99

Got: Time: 14147193 Phase: 2 Arm: 1299.062500 Main: 1741.262451 Alt: 1284.187500

RSSI: -99

Got: Time: 14147360 Phase: 2 Arm: 1299.062500 Main: 1741.262451 Alt: 1284.187500

RSSI: -104

Got: Time: 14147527 Phase: 2 Arm: 1299.062500 Main: 1741.262451 Alt: 1283.875000

RSSI: -104

Got: Time: 14147694 Phase: 2 Arm: 1299.062500 Main: 1741.262451 Alt: 1284.187500

RSSI: -104

Got: Time: 14147860 Phase: 2 Arm: 1299.062500 Main: 1741.262451 Alt: 1284.375000

RSSI: -104

Got: Time: 14148027 Phase: 2 Arm: 1299.062500 Main: 1741.262451 Alt: 1283.937500

RSSI: -100

Got: Time: 14148194 Phase: 2 Arm: 1299.062500 Main: 1741.262451 Alt: 1284.562500

RSSI: -100

Got: Time: 14148361 Phase: 2 Arm: 1299.062500 Main: 1741.262451 Alt: 1284.125000

RSSI: -104

Got: Time: 14148527 Phase: 2 Arm: 1299.062500 Main: 1741.262451 Alt: 1284.375000

RSSI: -104

Got: Time: 14148694 Phase: 2 Arm: 1299.062500 Main: 1741.262451 Alt: 1283.937500

RSSI: -104

Got: Time: 14148861 Phase: 2 Arm: 1299.062500 Main: 1741.262451 Alt: 1284.125000

RSSI: -104

Got: Time: 14149028 Phase: 2 Arm: 1299.062500 Main: 1741.262451 Alt: 1284.562500

RSSI: -100

Got: Time: 14149195 Phase: 2 Arm: 1299.062500 Main: 1741.262451 Alt: 1284.437500

RSSI: -101

Got: Time: 14149361 Phase: 2 Arm: 1299.062500 Main: 1741.262451 Alt: 1284.125000

RSSI: -101

Got: Time: 14149528 Phase: 2 Arm: 1299.062500 Main: 1741.262451 Alt: 1284.375000

RSSI: -104

Got: Time: 14149695 Phase: 2 Arm: 1299.062500 Main: 1741.262451 Alt: 1284.250000

RSSI: -104

Got: Time: 14149862 Phase: 2 Arm: 1299.062500 Main: 1741.262451 Alt: 1284.312500

RSSI: -104

Got: Time: 14150028 Phase: 2 Arm: 1299.062500 Main: 1741.262451 Alt: 1284.562500

RSSI: -100

Got: Time: 14150195 Phase: 2 Arm: 1299.062500 Main: 1741.262451 Alt: 1284.250000

RSSI: -100

Got: Time: 14150362 Phase: 2 Arm: 1299.062500 Main: 1741.262451 Alt: 1284.312500

RSSI: -104

Got: Time: 14150529 Phase: 2 Arm: 1299.062500 Main: 1741.262451 Alt: 1284.187500

RSSI: -104

Got: Time: 14150695 Phase: 2 Arm: 1299.062500 Main: 1741.262451 Alt: 1283.937500

RSSI: -104

Got: Time: 14150862 Phase: 2 Arm: 1299.062500 Main: 1741.262451 Alt: 1284.187500

RSSI: -104

Got: Time: 14151029 Phase: 2 Arm: 1299.062500 Main: 1741.262451 Alt: 1283.937500

RSSI: -101

Got: Time: 14151196 Phase: 2 Arm: 1299.062500 Main: 1741.262451 Alt: 1283.937500

RSSI: -100

Got: Time: 14151363 Phase: 2 Arm: 1299.062500 Main: 1741.262451 Alt: 1283.875000

RSSI: -105

Got: Time: 14151529 Phase: 2 Arm: 1299.062500 Main: 1741.262451 Alt: 1283.437500

RSSI: -104

Got: Time: 14151696 Phase: 2 Arm: 1299.062500 Main: 1741.262451 Alt: 1284.250000

RSSI: -104

Got: Time: 14151863 Phase: 2 Arm: 1299.062500 Main: 1741.262451 Alt: 1284.062500

RSSI: -105

Got: Time: 14152030 Phase: 2 Arm: 1299.062500 Main: 1741.262451 Alt: 1283.875000

RSSI: -100

Got: Time: 14152196 Phase: 2 Arm: 1299.062500 Main: 1741.262451 Alt: 1284.375000

RSSI: -103

Got: Time: 14152363 Phase: 2 Arm: 1299.062500 Main: 1741.262451 Alt: 1284.812500

RSSI: -105

Got: Time: 14152530 Phase: 2 Arm: 1299.062500 Main: 1741.262451 Alt: 1284.187500

RSSI: -106

Got: Time: 14152697 Phase: 2 Arm: 1299.062500 Main: 1741.262451 Alt: 1284.250000

RSSI: -106

Got: Time: 14152863 Phase: 2 Arm: 1299.062500 Main: 1741.262451 Alt: 1284.187500

RSSI: -105

Got: Time: 14153030 Phase: 2 Arm: 1299.062500 Main: 1741.262451 Alt: 1283.937500

RSSI: -102

Got: Time: 14153197 Phase: 2 Arm: 1299.062500 Main: 1741.262451 Alt: 1284.312500

RSSI: -105

Got: Time: 14153364 Phase: 2 Arm: 1299.062500 Main: 1741.262451 Alt: 1284.312500

RSSI: -106

Got: Time: 14153530 Phase: 2 Arm: 1299.062500 Main: 1741.262451 Alt: 1284.062500

RSSI: -106

Got: Time: 14153697 Phase: 2 Arm: 1299.062500 Main: 1741.262451 Alt: 1284.625000

RSSI: -106

Got: Time: 14153864 Phase: 2 Arm: 1299.062500 Main: 1741.262451 Alt: 1284.062500

RSSI: -106

Got: Time: 14154031 Phase: 2 Arm: 1299.062500 Main: 1741.262451 Alt: 1284.125000

RSSI: -101

Got: Time: 14154198 Phase: 2 Arm: 1299.062500 Main: 1741.262451 Alt: 1284.625000

RSSI: -101

Got: Time: 14154364 Phase: 2 Arm: 1299.062500 Main: 1741.262451 Alt: 1284.375000

RSSI: -102

Got: Time: 14154531 Phase: 2 Arm: 1299.062500 Main: 1741.262451 Alt: 1283.937500

RSSI: -105

Got: Time: 14154698 Phase: 2 Arm: 1299.062500 Main: 1741.262451 Alt: 1284.125000

RSSI: -106

Got: Time: 14154865 Phase: 2 Arm: 1299.062500 Main: 1741.262451 Alt: 1284.062500

RSSI: -106

Got: Time: 14155031 Phase: 2 Arm: 1299.062500 Main: 1741.262451 Alt: 1284.187500

RSSI: -100

Got: Time: 14155198 Phase: 2 Arm: 1299.062500 Main: 1741.262451 Alt: 1284.375000

RSSI: -105

Got: Time: 14155365 Phase: 2 Arm: 1299.062500 Main: 1741.262451 Alt: 1284.187500

RSSI: -106

Got: Time: 14155532 Phase: 2 Arm: 1299.062500 Main: 1741.262451 Alt: 1284.250000

RSSI: -105

Got: Time: 14155698 Phase: 2 Arm: 1299.062500 Main: 1741.262451 Alt: 1284.500000

RSSI: -106

Got: Time: 14155865 Phase: 2 Arm: 1299.062500 Main: 1741.262451 Alt: 1284.187500

RSSI: -106

Got: Time: 14156032 Phase: 2 Arm: 1299.062500 Main: 1741.262451 Alt: 1284.562500

RSSI: -100

Got: Time: 14156199 Phase: 2 Arm: 1299.062500 Main: 1741.262451 Alt: 1284.500000

RSSI: -105

Got: Time: 14156366 Phase: 2 Arm: 1299.062500 Main: 1741.262451 Alt: 1284.562500

RSSI: -105

Got: Time: 14156532 Phase: 2 Arm: 1299.062500 Main: 1741.262451 Alt: 1284.500000

RSSI: -106

Got: Time: 14156699 Phase: 2 Arm: 1299.062500 Main: 1741.262451 Alt: 1283.937500

RSSI: -106

Got: Time: 14156866 Phase: 2 Arm: 1299.062500 Main: 1741.262451 Alt: 1284.062500

RSSI: -106

Got: Time: 14157033 Phase: 2 Arm: 1299.062500 Main: 1741.262451 Alt: 1284.375000

RSSI: -100

Got: Time: 14157199 Phase: 2 Arm: 1299.062500 Main: 1741.262451 Alt: 1284.500000

RSSI: -105

Got: Time: 14157366 Phase: 2 Arm: 1299.062500 Main: 1741.262451 Alt: 1284.187500

RSSI: -105

Got: Time: 14157533 Phase: 2 Arm: 1299.062500 Main: 1741.262451 Alt: 1284.312500

RSSI: -105

Got: Time: 14157700 Phase: 2 Arm: 1299.062500 Main: 1741.262451 Alt: 1284.500000

RSSI: -105

Got: Time: 14157866 Phase: 2 Arm: 1299.062500 Main: 1741.262451 Alt: 1284.000000

RSSI: -106

Got: Time: 14158033 Phase: 2 Arm: 1299.062500 Main: 1741.262451 Alt: 1284.625000

RSSI: -103

Got: Time: 14158200 Phase: 2 Arm: 1299.062500 Main: 1741.262451 Alt: 1284.062500

RSSI: -103

Got: Time: 14158367 Phase: 2 Arm: 1299.062500 Main: 1741.262451 Alt: 1284.125000

RSSI: -106

Got: Time: 14158534 Phase: 2 Arm: 1299.062500 Main: 1741.262451 Alt: 1284.562500

RSSI: -106

Got: Time: 14158700 Phase: 2 Arm: 1299.062500 Main: 1741.262451 Alt: 1284.312500

RSSI: -106

Got: Time: 14158867 Phase: 2 Arm: 1299.062500 Main: 1741.262451 Alt: 1284.687500

RSSI: -106

Got: Time: 14159034 Phase: 2 Arm: 1299.062500 Main: 1741.262451 Alt: 1284.437500

RSSI: -102

Got: Time: 14159201 Phase: 2 Arm: 1299.062500 Main: 1741.262451 Alt: 1284.187500

RSSI: -102

Got: Time: 14159367 Phase: 2 Arm: 1299.062500 Main: 1741.262451 Alt: 1284.062500

RSSI: -102

Got: Time: 14159534 Phase: 2 Arm: 1299.062500 Main: 1741.262451 Alt: 1284.187500

RSSI: -106

Got: Time: 14159701 Phase: 2 Arm: 1299.062500 Main: 1741.262451 Alt: 1283.875000

RSSI: -106

Got: Time: 14159868 Phase: 2 Arm: 1299.062500 Main: 1741.262451 Alt: 1284.750000

RSSI: -106

Got: Time: 14160034 Phase: 2 Arm: 1299.062500 Main: 1741.262451 Alt: 1284.562500

RSSI: -102

Got: Time: 14160201 Phase: 2 Arm: 1299.062500 Main: 1741.262451 Alt: 1284.312500

RSSI: -103

Got: Time: 14160368 Phase: 2 Arm: 1299.062500 Main: 1741.262451 Alt: 1284.187500

RSSI: -106

Got: Time: 14160535 Phase: 2 Arm: 1299.062500 Main: 1741.262451 Alt: 1284.437500

RSSI: -106

Got: Time: 14160701 Phase: 2 Arm: 1299.062500 Main: 1741.262451 Alt: 1284.250000

RSSI: -106

Got: Time: 14160868 Phase: 2 Arm: 1299.062500 Main: 1741.262451 Alt: 1284.375000

RSSI: -106

Got: Time: 14161035 Phase: 2 Arm: 1299.062500 Main: 1741.262451 Alt: 1284.500000

RSSI: -104

Got: Time: 14161202 Phase: 2 Arm: 1299.062500 Main: 1741.262451 Alt: 1284.375000

RSSI: -106

Got: Time: 14161369 Phase: 2 Arm: 1299.062500 Main: 1741.262451 Alt: 1284.062500

RSSI: -106

Got: Time: 14161535 Phase: 2 Arm: 1299.062500 Main: 1741.262451 Alt: 1284.500000

RSSI: -107

Got: Time: 14161702 Phase: 2 Arm: 1299.062500 Main: 1741.262451 Alt: 1284.375000

RSSI: -106

Got: Time: 14161869 Phase: 2 Arm: 1299.062500 Main: 1741.262451 Alt: 1284.312500

RSSI: -106

Got: Time: 14162036 Phase: 2 Arm: 1299.062500 Main: 1741.262451 Alt: 1284.500000

RSSI: -104

Got: Time: 14162202 Phase: 2 Arm: 1299.062500 Main: 1741.262451 Alt: 1284.562500

RSSI: -105

Got: Time: 14162369 Phase: 2 Arm: 1299.062500 Main: 1741.262451 Alt: 1284.875000

RSSI: -106

Got: Time: 14162536 Phase: 2 Arm: 1299.062500 Main: 1741.262451 Alt: 1284.187500

RSSI: -106

Got: Time: 14162703 Phase: 2 Arm: 1299.062500 Main: 1741.262451 Alt: 1284.500000

RSSI: -106

Got: Time: 14162869 Phase: 2 Arm: 1299.062500 Main: 1741.262451 Alt: 1284.375000

RSSI: -106

Got: Time: 14163036 Phase: 2 Arm: 1299.062500 Main: 1741.262451 Alt: 1284.000000

RSSI: -103

Got: Time: 14163203 Phase: 2 Arm: 1299.062500 Main: 1741.262451 Alt: 1284.125000

RSSI: -105

Got: Time: 14163370 Phase: 2 Arm: 1299.062500 Main: 1741.262451 Alt: 1284.562500

RSSI: -106

Got: Time: 14163537 Phase: 2 Arm: 1299.062500 Main: 1741.262451 Alt: 1284.187500

RSSI: -106

Got: Time: 14163703 Phase: 2 Arm: 1299.062500 Main: 1741.262451 Alt: 1284.312500

RSSI: -106

Got: Time: 14163870 Phase: 2 Arm: 1299.062500 Main: 1741.262451 Alt: 1283.937500

RSSI: -107

Got: Time: 14164037 Phase: 2 Arm: 1299.062500 Main: 1741.262451 Alt: 1284.187500

RSSI: -102

Got: Time: 14164204 Phase: 2 Arm: 1299.062500 Main: 1741.262451 Alt: 1284.187500

RSSI: -104

Got: Time: 14164370 Phase: 2 Arm: 1299.062500 Main: 1741.262451 Alt: 1284.062500

RSSI: -103

Got: Time: 14164537 Phase: 2 Arm: 1299.062500 Main: 1741.262451 Alt: 1284.187500

RSSI: -106

Got: Time: 14164704 Phase: 2 Arm: 1299.062500 Main: 1741.262451 Alt: 1284.375000

RSSI: -106

Got: Time: 14164871 Phase: 2 Arm: 1299.062500 Main: 1741.262451 Alt: 1283.937500

RSSI: -106

Got: Time: 14165037 Phase: 2 Arm: 1299.062500 Main: 1741.262451 Alt: 1284.562500

RSSI: -103

Got: Time: 14165204 Phase: 2 Arm: 1299.062500 Main: 1741.262451 Alt: 1284.437500

RSSI: -104

Got: Time: 14165371 Phase: 2 Arm: 1299.062500 Main: 1741.262451 Alt: 1284.375000

RSSI: -106

Got: Time: 14165538 Phase: 2 Arm: 1299.062500 Main: 1741.262451 Alt: 1284.000000

RSSI: -106

Got: Time: 14165705 Phase: 2 Arm: 1299.062500 Main: 1741.262451 Alt: 1283.937500

RSSI: -106

Got: Time: 14165871 Phase: 2 Arm: 1299.062500 Main: 1741.262451 Alt: 1284.812500

RSSI: -107

Got: Time: 14166038 Phase: 2 Arm: 1299.062500 Main: 1741.262451 Alt: 1284.062500

RSSI: -104

Got: Time: 14166205 Phase: 2 Arm: 1299.062500 Main: 1741.262451 Alt: 1284.062500

RSSI: -102

Got: Time: 14166372 Phase: 2 Arm: 1299.062500 Main: 1741.262451 Alt: 1284.562500

RSSI: -107

Got: Time: 14166538 Phase: 2 Arm: 1299.062500 Main: 1741.262451 Alt: 1284.562500

RSSI: -106

Got: Time: 14166705 Phase: 2 Arm: 1299.062500 Main: 1741.262451 Alt: 1284.937500

RSSI: -106

Got: Time: 14166872 Phase: 2 Arm: 1299.062500 Main: 1741.262451 Alt: 1284.000000

RSSI: -107

Got: Time: 14167039 Phase: 2 Arm: 1299.062500 Main: 1741.262451 Alt: 1284.312500

RSSI: -104

Got: Time: 14167205 Phase: 2 Arm: 1299.062500 Main: 1741.262451 Alt: 1283.937500

RSSI: -103

Got: Time: 14167372 Phase: 2 Arm: 1299.062500 Main: 1741.262451 Alt: 1284.312500

RSSI: -106

Got: Time: 14167539 Phase: 2 Arm: 1299.062500 Main: 1741.262451 Alt: 1284.375000

RSSI: -107

Got: Time: 14167706 Phase: 2 Arm: 1299.062500 Main: 1741.262451 Alt: 1284.375000

RSSI: -106

Got: Time: 14167872 Phase: 2 Arm: 1299.062500 Main: 1741.262451 Alt: 1284.687500

RSSI: -107

Got: Time: 14168039 Phase: 2 Arm: 1299.062500 Main: 1741.262451 Alt: 1284.562500

RSSI: -102

Got: Time: 14168206 Phase: 2 Arm: 1299.062500 Main: 1741.262451 Alt: 1284.312500

RSSI: -102

Got: Time: 14168373 Phase: 2 Arm: 1299.062500 Main: 1741.262451 Alt: 1284.500000

RSSI: -106

Got: Time: 14168540 Phase: 2 Arm: 1299.062500 Main: 1741.262451 Alt: 1283.875000

RSSI: -106

Got: Time: 14168706 Phase: 2 Arm: 1299.062500 Main: 1741.262451 Alt: 1284.000000

RSSI: -106

Got: Time: 14168873 Phase: 2 Arm: 1299.062500 Main: 1741.262451 Alt: 1284.562500

RSSI: -106

Got: Time: 14169040 Phase: 2 Arm: 1299.062500 Main: 1741.262451 Alt: 1284.187500

RSSI: -105

Got: Time: 14169207 Phase: 2 Arm: 1299.062500 Main: 1741.262451 Alt: 1284.125000

RSSI: -102

Got: Time: 14169373 Phase: 2 Arm: 1299.062500 Main: 1741.262451 Alt: 1284.125000

RSSI: -102

Got: Time: 14169540 Phase: 2 Arm: 1299.062500 Main: 1741.262451 Alt: 1284.500000

RSSI: -106

Got: Time: 14169707 Phase: 2 Arm: 1299.062500 Main: 1741.262451 Alt: 1284.375000

RSSI: -107

Got: Time: 14169874 Phase: 2 Arm: 1299.062500 Main: 1741.262451 Alt: 1284.812500

RSSI: -107

Got: Time: 14170040 Phase: 2 Arm: 1299.062500 Main: 1741.262451 Alt: 1284.437500

RSSI: -102

Got: Time: 14170207 Phase: 2 Arm: 1299.062500 Main: 1741.262451 Alt: 1284.687500

RSSI: -102

Got: Time: 14170374 Phase: 2 Arm: 1299.062500 Main: 1741.262451 Alt: 1284.125000

RSSI: -106

Got: Time: 14170541 Phase: 2 Arm: 1299.062500 Main: 1741.262451 Alt: 1284.562500

RSSI: -107

Got: Time: 14170708 Phase: 2 Arm: 1299.062500 Main: 1741.262451 Alt: 1284.750000

RSSI: -107

Got: Time: 14170874 Phase: 2 Arm: 1299.062500 Main: 1741.262451 Alt: 1284.687500

RSSI: -106

Got: Time: 14171041 Phase: 2 Arm: 1299.062500 Main: 1741.262451 Alt: 1284.250000

RSSI: -101

Got: Time: 14171208 Phase: 2 Arm: 1299.062500 Main: 1741.262451 Alt: 1284.375000

RSSI: -106

Got: Time: 14171375 Phase: 2 Arm: 1299.062500 Main: 1741.262451 Alt: 1283.937500

RSSI: -107

Got: Time: 14171541 Phase: 2 Arm: 1299.062500 Main: 1741.262451 Alt: 1284.125000

RSSI: -107

Got: Time: 14171708 Phase: 2 Arm: 1299.062500 Main: 1741.262451 Alt: 1284.437500

RSSI: -107

Got: Time: 14171875 Phase: 2 Arm: 1299.062500 Main: 1741.262451 Alt: 1284.187500

RSSI: -107

Got: Time: 14172042 Phase: 2 Arm: 1299.062500 Main: 1741.262451 Alt: 1284.375000

RSSI: -105

Got: Time: 14172208 Phase: 2 Arm: 1299.062500 Main: 1741.262451 Alt: 1284.500000

RSSI: -102

Got: Time: 14172375 Phase: 2 Arm: 1299.062500 Main: 1741.262451 Alt: 1283.937500

RSSI: -106

Got: Time: 14172542 Phase: 2 Arm: 1299.062500 Main: 1741.262451 Alt: 1284.125000

RSSI: -106

Got: Time: 14172709 Phase: 2 Arm: 1299.062500 Main: 1741.262451 Alt: 1284.437500

RSSI: -107

Got: Time: 14172876 Phase: 2 Arm: 1299.062500 Main: 1741.262451 Alt: 1284.437500

RSSI: -107

Got: Time: 14173042 Phase: 2 Arm: 1299.062500 Main: 1741.262451 Alt: 1284.562500

RSSI: -103

Got: Time: 14173209 Phase: 2 Arm: 1299.062500 Main: 1741.262451 Alt: 1283.875000

RSSI: -103

Got: Time: 14173376 Phase: 2 Arm: 1299.062500 Main: 1741.262451 Alt: 1284.375000

RSSI: -107

Got: Time: 14173543 Phase: 2 Arm: 1299.062500 Main: 1741.262451 Alt: 1284.625000

RSSI: -106

Got: Time: 14173709 Phase: 2 Arm: 1299.062500 Main: 1741.262451 Alt: 1283.937500

RSSI: -106

Got: Time: 14173876 Phase: 2 Arm: 1299.062500 Main: 1741.262451 Alt: 1284.812500

RSSI: -107

Got: Time: 14174043 Phase: 2 Arm: 1299.062500 Main: 1741.262451 Alt: 1284.562500

RSSI: -103

Got: Time: 14174210 Phase: 2 Arm: 1299.062500 Main: 1741.262451 Alt: 1284.062500

RSSI: -102

Got: Time: 14174376 Phase: 2 Arm: 1299.062500 Main: 1741.262451 Alt: 1284.000000

RSSI: -102

Got: Time: 14174543 Phase: 2 Arm: 1299.062500 Main: 1741.262451 Alt: 1284.312500

RSSI: -107

Got: Time: 14174710 Phase: 2 Arm: 1299.062500 Main: 1741.262451 Alt: 1284.375000

RSSI: -106

Got: Time: 14174877 Phase: 2 Arm: 1299.062500 Main: 1741.262451 Alt: 1284.375000

RSSI: -106

Got: Time: 14175043 Phase: 2 Arm: 1299.062500 Main: 1741.262451 Alt: 1284.187500

RSSI: -103

Got: Time: 14175210 Phase: 2 Arm: 1299.062500 Main: 1741.262451 Alt: 1284.187500

RSSI: -103

Got: Time: 14175377 Phase: 2 Arm: 1299.062500 Main: 1741.262451 Alt: 1284.562500

RSSI: -107

Got: Time: 14175544 Phase: 2 Arm: 1299.062500 Main: 1741.262451 Alt: 1284.250000

RSSI: -106

Got: Time: 14175711 Phase: 2 Arm: 1299.062500 Main: 1741.262451 Alt: 1283.875000

RSSI: -106

Got: Time: 14175877 Phase: 2 Arm: 1299.062500 Main: 1741.262451 Alt: 1284.687500

RSSI: -107

Got: Time: 14176044 Phase: 2 Arm: 1299.062500 Main: 1741.262451 Alt: 1284.062500

RSSI: -104

Got: Time: 14176211 Phase: 2 Arm: 1299.062500 Main: 1741.262451 Alt: 1284.125000

RSSI: -103

Got: Time: 14176378 Phase: 2 Arm: 1299.062500 Main: 1741.262451 Alt: 1284.125000

RSSI: -106

Got: Time: 14176544 Phase: 2 Arm: 1299.062500 Main: 1741.262451 Alt: 1284.062500

RSSI: -107

Got: Time: 14176711 Phase: 2 Arm: 1299.062500 Main: 1741.262451 Alt: 1284.375000

RSSI: -107

Got: Time: 14176878 Phase: 2 Arm: 1299.062500 Main: 1741.262451 Alt: 1283.500000

RSSI: -106

Got: Time: 14177045 Phase: 2 Arm: 1299.062500 Main: 1741.262451 Alt: 1283.937500

RSSI: -104

Got: Time: 14177211 Phase: 2 Arm: 1299.062500 Main: 1741.262451 Alt: 1284.500000

RSSI: -104

Got: Time: 14177378 Phase: 2 Arm: 1299.062500 Main: 1741.262451 Alt: 1284.812500

RSSI: -106

Got: Time: 14177545 Phase: 2 Arm: 1299.062500 Main: 1741.262451 Alt: 1284.125000

RSSI: -107

Got: Time: 14177712 Phase: 2 Arm: 1299.062500 Main: 1741.262451 Alt: 1284.437500

RSSI: -106

Got: Time: 14177879 Phase: 2 Arm: 1299.062500 Main: 1741.262451 Alt: 1284.000000

RSSI: -107

Got: Time: 14178045 Phase: 2 Arm: 1299.062500 Main: 1741.262451 Alt: 1284.187500

RSSI: -104

Got: Time: 14178212 Phase: 2 Arm: 1299.062500 Main: 1741.262451 Alt: 1284.375000

RSSI: -103

Got: Time: 14178379 Phase: 2 Arm: 1299.062500 Main: 1741.262451 Alt: 1284.875000

RSSI: -107

Got: Time: 14178546 Phase: 2 Arm: 1299.062500 Main: 1741.262451 Alt: 1284.312500

RSSI: -106

Got: Time: 14178712 Phase: 2 Arm: 1299.062500 Main: 1741.262451 Alt: 1283.812500

RSSI: -107

Got: Time: 14178879 Phase: 2 Arm: 1299.062500 Main: 1741.262451 Alt: 1284.500000

RSSI: -106

Got: Time: 14179046 Phase: 2 Arm: 1299.062500 Main: 1741.262451 Alt: 1284.812500

RSSI: -103

Got: Time: 14179213 Phase: 2 Arm: 1299.062500 Main: 1741.262451 Alt: 1283.937500

RSSI: -104

Got: Time: 14179379 Phase: 2 Arm: 1299.062500 Main: 1741.262451 Alt: 1284.500000

RSSI: -103

Got: Time: 14179546 Phase: 2 Arm: 1299.062500 Main: 1741.262451 Alt: 1283.687500

RSSI: -107

Got: Time: 14179713 Phase: 2 Arm: 1299.062500 Main: 1741.262451 Alt: 1284.125000

RSSI: -107

Got: Time: 14179880 Phase: 2 Arm: 1299.062500 Main: 1741.262451 Alt: 1284.937500

RSSI: -107

Got: Time: 14180047 Phase: 2 Arm: 1299.062500 Main: 1741.262451 Alt: 1283.750000

RSSI: -104

Got: Time: 14180213 Phase: 2 Arm: 1299.062500 Main: 1741.262451 Alt: 1284.187500

RSSI: -104

Got: Time: 14180380 Phase: 2 Arm: 1299.062500 Main: 1741.262451 Alt: 1284.062500

RSSI: -106

Got: Time: 14180547 Phase: 2 Arm: 1299.062500 Main: 1741.262451 Alt: 1284.562500

RSSI: -107

Got: Time: 14180714 Phase: 2 Arm: 1299.062500 Main: 1741.262451 Alt: 1284.375000

RSSI: -109

Got: Time: 14180880 Phase: 2 Arm: 1299.062500 Main: 1741.262451 Alt: 1284.625000

RSSI: -102

Got: Time: 14181047 Phase: 2 Arm: 1299.062500 Main: 1741.262451 Alt: 1285.625000

RSSI: -99

Got: Time: 14181214 Phase: 2 Arm: 1299.062500 Main: 1741.262451 Alt: 1288.750000

RSSI: -95

Got: Time: 14181381 Phase: 2 Arm: 1299.062500 Main: 1741.262451 Alt: 1296.500000

RSSI: -98

Got: Time: 14181381 Phase: 3 alt: 1308.000000

RSSI: -104

Got: Time: 14181716 Phase: 3 alt: 1323.687500

RSSI: -96

Got: Time: 14181885 Phase: 3 alt: 1341.312500

RSSI: -97

Got: Time: 14182055 Phase: 3 alt: 1361.750000

RSSI: -97

Got: Time: 14182225 Phase: 3 alt: 1383.375000

RSSI: -92

Got: Time: 14182394 Phase: 3 alt: 1415.125000

RSSI: -93

Got: Time: 14182565 Phase: 3 alt: 1443.687500

RSSI: -96

Got: Time: 14182733 Phase: 3 alt: 1477.812500

RSSI: -96

Got: Time: 14182904 Phase: 3 alt: 1509.125000

RSSI: -92

Got: Time: 14183075 Phase: 3 alt: 1544.750000

RSSI: -91

Got: Time: 14183244 Phase: 3 alt: 1569.625000

RSSI: -90

Got: Time: 14183414 Phase: 3 alt: 1615.812500

RSSI: -93

Got: Time: 14183583 Phase: 3 alt: 1651.312500

RSSI: -96

Got: Time: 14183753 Phase: 3 alt: 1687.562500

RSSI: -96

Got: Time: 14183922 Phase: 3 alt: 1724.562500

RSSI: -96

Got: Time: 14184091 Phase: 3 alt: 1759.562500

RSSI: -95

Got: Time: 14184260 Phase: 3 alt: 1785.812500

RSSI: -90

Got: Time: 14184430 Phase: 3 alt: 1828.500000

RSSI: -90

Got: Time: 14184598 Phase: 3 alt: 1867.500000

RSSI: -90

Got: Time: 14184769 Phase: 3 alt: 1907.812500

RSSI: -90

Got: Time: 14184938 Phase: 3 alt: 1945.375000

RSSI: -90

Got: Time: 14185108 Phase: 3 alt: 1980.687500

RSSI: -89

Got: Time: 14185279 Phase: 3 alt: 2001.187500

RSSI: -92

Got: Time: 14185448 Phase: 3 alt: 2043.875000

RSSI: -91

Got: Time: 14185619 Phase: 3 alt: 2074.437500

RSSI: -92

Got: Time: 14185787 Phase: 3 alt: 2105.875000

RSSI: -92

Got: Time: 14185958 Phase: 3 alt: 2134.812500

RSSI: -93

Got: Time: 14186128 Phase: 3 alt: 2165.375000

RSSI: -92

Got: Time: 14186297 Phase: 3 alt: 2192.000000

RSSI: -95

Got: Time: 14186465 Phase: 3 alt: 2220.875000

RSSI: -95

Got: Time: 14186634 Phase: 3 alt: 2246.625000

RSSI: -93

Got: Time: 14186803 Phase: 3 alt: 2272.062500

RSSI: -95

Got: Time: 14186973 Phase: 3 alt: 2298.500000

RSSI: -96

Got: Time: 14187142 Phase: 3 alt: 2325.187500

RSSI: -95

Got: Time: 14187313 Phase: 3 alt: 2350.687500

RSSI: -98

Got: Time: 14187484 Phase: 3 alt: 2376.312500

RSSI: -100

Got: Time: 14187653 Phase: 3 alt: 2401.125000

RSSI: -101

Got: Time: 14187823 Phase: 3 alt: 2426.125000

RSSI: -101

Got: Time: 14187992 Phase: 3 alt: 2448.937500

RSSI: -99

Got: Time: 14188163 Phase: 3 alt: 2472.875000

RSSI: -92

Got: Time: 14188502 Phase: 3 alt: 2521.375000

RSSI: -96

Got: Time: 14188673 Phase: 3 alt: 2541.625000

RSSI: -95

Got: Time: 14188841 Phase: 3 alt: 2566.312500

RSSI: -96

Got: Time: 14189010 Phase: 3 alt: 2587.437500

RSSI: -96

Got: Time: 14189179 Phase: 3 alt: 2607.750000

RSSI: -92

Got: Time: 14189347 Phase: 3 alt: 2629.687500

RSSI: -92

Got: Time: 14189518 Phase: 3 alt: 2649.375000

RSSI: -95

Got: Time: 14189688 Phase: 3 alt: 2668.812500

RSSI: -95

Got: Time: 14189857 Phase: 3 alt: 2689.437500

RSSI: -96

Got: Time: 14190028 Phase: 3 alt: 2710.250000

RSSI: -92

Got: Time: 14190196 Phase: 3 alt: 2728.625000

RSSI: -93

Got: Time: 14190367 Phase: 3 alt: 2750.000000

RSSI: -96

Got: Time: 14190538 Phase: 3 alt: 2769.625000

RSSI: -96

Got: Time: 14190707 Phase: 3 alt: 2786.937500

RSSI: -97

Got: Time: 14190877 Phase: 3 alt: 2808.250000

RSSI: -97

Got: Time: 14191046 Phase: 3 alt: 2825.062500

RSSI: -95

Got: Time: 14191216 Phase: 3 alt: 2839.937500

RSSI: -96

Got: Time: 14191386 Phase: 3 alt: 2859.937500

RSSI: -99

Got: Time: 14191555 Phase: 3 alt: 2876.000000

RSSI: -99

Got: Time: 14191723 Phase: 3 alt: 2893.000000

RSSI: -100

Got: Time: 14191893 Phase: 3 alt: 2910.062500

RSSI: -100

Got: Time: 14192062 Phase: 3 alt: 2925.562500

RSSI: -98

Got: Time: 14192232 Phase: 3 alt: 2941.500000

RSSI: -99

Got: Time: 14192401 Phase: 3 alt: 2958.750000

RSSI: -102

Got: Time: 14192572 Phase: 3 alt: 2973.875000

RSSI: -102

Got: Time: 14192743 Phase: 3 alt: 2987.562500

RSSI: -102

Got: Time: 14192911 Phase: 3 alt: 3001.625000

RSSI: -103

Got: Time: 14193082 Phase: 3 alt: 3016.250000

RSSI: -103

Got: Time: 14193251 Phase: 3 alt: 3025.125000

RSSI: -103

Got: Time: 14193421 Phase: 3 alt: 3043.312500

RSSI: -106

Got: Time: 14193592 Phase: 3 alt: 3055.500000

RSSI: -106

Got: Time: 14193761 Phase: 3 alt: 3068.812500

RSSI: -105

Got: Time: 14193931 Phase: 3 alt: 3083.562500

RSSI: -104

Got: Time: 14194100 Phase: 3 alt: 3095.812500

RSSI: -102

Got: Time: 14194268 Phase: 3 alt: 3107.500000

RSSI: -103

Got: Time: 14194437 Phase: 3 alt: 3118.687500

RSSI: -101

Got: Time: 14194606 Phase: 3 alt: 3130.000000

RSSI: -105

Got: Time: 14194776 Phase: 3 alt: 3141.562500

RSSI: -105

Got: Time: 14194947 Phase: 3 alt: 3151.312500

RSSI: -104

Got: Time: 14195116 Phase: 3 alt: 3163.125000

RSSI: -104

Got: Time: 14195286 Phase: 3 alt: 3172.437500

RSSI: -104

Got: Time: 14195455 Phase: 3 alt: 3185.187500

RSSI: -104

Got: Time: 14195626 Phase: 3 alt: 3194.437500

RSSI: -104

Got: Time: 14195796 Phase: 3 alt: 3204.875000

RSSI: -103

Got: Time: 14195965 Phase: 3 alt: 3213.750000

RSSI: -104

Got: Time: 14196136 Phase: 3 alt: 3223.062500

RSSI: -100

Got: Time: 14196304 Phase: 3 alt: 3231.750000

RSSI: -103

Got: Time: 14196474 Phase: 3 alt: 3239.187500

RSSI: -103

Got: Time: 14196642 Phase: 3 alt: 3248.062500

RSSI: -103

Got: Time: 14196811 Phase: 3 alt: 3255.250000

RSSI: -102

Got: Time: 14196981 Phase: 3 alt: 3263.687500

RSSI: -101

Got: Time: 14197151 Phase: 3 alt: 3272.812500

RSSI: -99

Got: Time: 14197320 Phase: 3 alt: 3279.875000

RSSI: -101

Got: Time: 14197490 Phase: 3 alt: 3286.812500

RSSI: -101

Got: Time: 14197659 Phase: 3 alt: 3293.375000

RSSI: -101

Got: Time: 14197830 Phase: 3 alt: 3299.750000

RSSI: -100

Got: Time: 14198001 Phase: 3 alt: 3305.687500

RSSI: -100

Got: Time: 14198169 Phase: 3 alt: 3311.250000

RSSI: -99

Got: Time: 14198340 Phase: 3 alt: 3316.312500

RSSI: -101

Got: Time: 14198509 Phase: 3 alt: 3322.187500

RSSI: -101

Got: Time: 14198678 Phase: 3 alt: 3326.937500

RSSI: -102

Got: Time: 14198847 Phase: 3 alt: 3332.625000

RSSI: -102

Got: Time: 14199015 Phase: 3 alt: 3338.937500

RSSI: -103

Got: Time: 14199185 Phase: 3 alt: 3343.500000

RSSI: -102

Got: Time: 14199355 Phase: 3 alt: 3347.562500

RSSI: -104

Got: Time: 14199523 Phase: 3 alt: 3351.687500

RSSI: -111

Got: Time: 14199694 Phase: 3 alt: 3355.500000

RSSI: -111

Got: Time: 14199863 Phase: 3 alt: 3358.625000

RSSI: -108

Got: Time: 14200034 Phase: 3 alt: 3362.250000

RSSI: -100

Got: Time: 14201256 Phase: 4 alt: 3380.187500

RSSI: -104

Got: Time: 14201425 Phase: 4 alt: 3381.562500

RSSI: -108

Got: Time: 14201596 Phase: 4 alt: 3382.000000

RSSI: -107

Got: Time: 14201764 Phase: 4 alt: 3383.000000

RSSI: -107

Got: Time: 14201934 Phase: 4 alt: 3382.625000

RSSI: -106

Got: Time: 14202104 Phase: 4 alt: 3382.750000

RSSI: -105

Got: Time: 14202272 Phase: 4 alt: 3382.625000

RSSI: -115

Got: Time: 14202441 Phase: 4 alt: 3371.250000

RSSI: -114

Got: Time: 14202611 Phase: 4 alt: 3381.687500

RSSI: -109

Got: Time: 14202780 Phase: 4 alt: 3381.312500

RSSI: -119

Got: Time: 14202950 Phase: 4 alt: 3381.062500

RSSI: -129

Got: Time: 14203119 Phase: 4 alt: 3381.437500

RSSI: -108

Got: Time: 14203290 Phase: 4 alt: 3379.937500

RSSI: -113

Got: Time: 14203461 Phase: 4 alt: 3379.125000

RSSI: -114

Got: Time: 14203800 Phase: 4 alt: 3377.187500

RSSI: -103

Got: Time: 14203969 Phase: 4 alt: 3375.375000

RSSI: -102

Got: Time: 14204139 Phase: 4 alt: 3375.250000

RSSI: -100

Got: Time: 14204309 Phase: 4 alt: 3381.000000

RSSI: -95

Got: Time: 14204478 Phase: 4 alt: 3385.062500

RSSI: -96

Got: Time: 14204646 Phase: 4 alt: 3372.125000

RSSI: -101

Got: Time: 14204815 Phase: 4 alt: 3365.625000

RSSI: -106

Got: Time: 14204985 Phase: 4 alt: 3366.125000

RSSI: -104

Got: Time: 14205154 Phase: 4 alt: 3359.687500

RSSI: -102

Got: Time: 14205494 Phase: 4 alt: 3353.750000

RSSI: -107

Got: Time: 14205665 Phase: 4 alt: 3346.562500

RSSI: -104

Got: Time: 14205834 Phase: 4 alt: 3345.625000

RSSI: -102

Got: Time: 14206004 Phase: 4 alt: 3339.125000

RSSI: -106

Got: Time: 14206344 Phase: 4 alt: 3328.562500

RSSI: -105

Got: Time: 14206514 Phase: 4 alt: 3339.500000

RSSI: -114

Got: Time: 14206683 Phase: 4 alt: 3327.375000

RSSI: -112

Got: Time: 14206853 Phase: 4 alt: 3314.312500

RSSI: -96

Got: Time: 14207022 Phase: 4 alt: 3330.625000

RSSI: -92

Got: Time: 14207191 Phase: 4 alt: 3318.687500

RSSI: -95

Got: Time: 14207359 Phase: 4 alt: 3320.937500

RSSI: -102

Got: Time: 14207528 Phase: 4 alt: 3314.500000

RSSI: -102

Got: Time: 14207699 Phase: 4 alt: 3308.312500

RSSI: -113

Got: Time: 14207869 Phase: 4 alt: 3303.187500

RSSI: -101

Got: Time: 14208038 Phase: 4 alt: 3293.250000

RSSI: -100

Got: Time: 14208209 Phase: 4 alt: 3287.125000

RSSI: -98

Got: Time: 14208377 Phase: 4 alt: 3288.687500

RSSI: -102

Got: Time: 14208548 Phase: 4 alt: 3285.250000

RSSI: -105

Got: Time: 14208719 Phase: 4 alt: 3286.750000

RSSI: -100

Got: Time: 14208888 Phase: 4 alt: 3280.375000

RSSI: -101

Got: Time: 14209058 Phase: 4 alt: 3277.062500

RSSI: -95

Got: Time: 14209227 Phase: 4 alt: 3271.500000

RSSI: -99

Got: Time: 14209396 Phase: 4 alt: 3260.375000

RSSI: -97

Got: Time: 14209565 Phase: 4 alt: 3256.062500

RSSI: -102

Got: Time: 14209734 Phase: 4 alt: 3270.312500

RSSI: -104

Got: Time: 14209903 Phase: 4 alt: 3256.562500

RSSI: -103

Got: Time: 14210073 Phase: 4 alt: 3248.812500

RSSI: -99

Got: Time: 14210413 Phase: 4 alt: 3247.000000

RSSI: -116

Got: Time: 14210581 Phase: 4 alt: 3248.937500

RSSI: -106

Got: Time: 14210752 Phase: 4 alt: 3245.187500

RSSI: -99

Got: Time: 14210923 Phase: 4 alt: 3229.562500

RSSI: -97

Got: Time: 14211092 Phase: 4 alt: 3220.750000

RSSI: -103

Got: Time: 14211262 Phase: 4 alt: 3223.062500

RSSI: -105

Got: Time: 14211431 Phase: 4 alt: 3223.562500

RSSI: -102

Got: Time: 14211601 Phase: 4 alt: 3224.375000

RSSI: -112

Got: Time: 14211770 Phase: 4 alt: 3217.625000

RSSI: -95

Got: Time: 14211939 Phase: 4 alt: 3213.687500

RSSI: -107

Got: Time: 14212277 Phase: 4 alt: 3197.187500

RSSI: -106

Got: Time: 14212447 Phase: 4 alt: 3188.312500

RSSI: -100

Got: Time: 14212617 Phase: 4 alt: 3179.062500

RSSI: -103

Got: Time: 14212786 Phase: 4 alt: 3175.000000

RSSI: -96

Got: Time: 14212956 Phase: 4 alt: 3167.875000

RSSI: -101

Got: Time: 14213127 Phase: 4 alt: 3168.750000

RSSI: -97

Got: Time: 14213296 Phase: 4 alt: 3174.187500

RSSI: -106

Got: Time: 14213466 Phase: 4 alt: 3170.062500

RSSI: -97

Got: Time: 14213635 Phase: 4 alt: 3151.437500

RSSI: -108

Got: Time: 14213805 Phase: 4 alt: 3153.500000

RSSI: -105

Got: Time: 14213976 Phase: 4 alt: 3151.375000

RSSI: -96

Got: Time: 14214144 Phase: 4 alt: 3137.875000

RSSI: -89

Got: Time: 14214313 Phase: 4 alt: 3131.437500

RSSI: -88

Got: Time: 14214482 Phase: 4 alt: 3130.312500

RSSI: -95

Got: Time: 14214651 Phase: 4 alt: 3126.312500

RSSI: -95

Got: Time: 14214821 Phase: 4 alt: 3128.562500

RSSI: -97

Got: Time: 14214990 Phase: 4 alt: 3125.875000

RSSI: -95

Got: Time: 14215332 Phase: 4 alt: 3118.750000

RSSI: -100

Got: Time: 14215500 Phase: 4 alt: 3117.437500

RSSI: -104

Got: Time: 14215671 Phase: 4 alt: 3110.750000

RSSI: -98

Got: Time: 14215840 Phase: 4 alt: 3097.375000

RSSI: -97

Got: Time: 14216010 Phase: 4 alt: 3089.437500

RSSI: -102

Got: Time: 14216181 Phase: 4 alt: 3092.875000

RSSI: -97

Got: Time: 14216350 Phase: 4 alt: 3092.437500

RSSI: -99

Got: Time: 14216520 Phase: 4 alt: 3088.250000

RSSI: -99

Got: Time: 14216689 Phase: 4 alt: 3085.562500

RSSI: -99

Got: Time: 14216857 Phase: 4 alt: 3077.562500

RSSI: -101

Got: Time: 14217026 Phase: 4 alt: 3064.625000

RSSI: -91

Got: Time: 14217195 Phase: 4 alt: 3058.812500

RSSI: -93

Got: Time: 14217365 Phase: 4 alt: 3065.750000

RSSI: -95

Got: Time: 14217536 Phase: 4 alt: 3064.500000

RSSI: -95

Got: Time: 14217705 Phase: 4 alt: 3055.250000

RSSI: -96

Got: Time: 14217876 Phase: 4 alt: 3057.750000

RSSI: -100

Got: Time: 14218045 Phase: 4 alt: 3050.500000

RSSI: -95

Got: Time: 14218386 Phase: 4 alt: 3027.562500

RSSI: -111

Got: Time: 14218555 Phase: 4 alt: 3031.125000

RSSI: -101

Got: Time: 14218726 Phase: 4 alt: 3031.875000

RSSI: -97

Got: Time: 14218894 Phase: 4 alt: 3031.250000

RSSI: -101

Got: Time: 14219064 Phase: 4 alt: 3031.437500

RSSI: -98

Got: Time: 14219234 Phase: 4 alt: 3032.187500

RSSI: -102

Got: Time: 14219741 Phase: 4 alt: 3007.875000

RSSI: -100

Got: Time: 14219910 Phase: 4 alt: 3003.875000

RSSI: -91

Got: Time: 14220080 Phase: 4 alt: 2989.687500

RSSI: -101

Got: Time: 14220249 Phase: 4 alt: 2981.125000

RSSI: -103

Got: Time: 14220420 Phase: 4 alt: 2984.437500

RSSI: -109

Got: Time: 14220591 Phase: 4 alt: 2979.437500

RSSI: -113

Got: Time: 14220760 Phase: 4 alt: 2979.500000

RSSI: -113

Got: Time: 14220930 Phase: 4 alt: 2975.000000

RSSI: -102

Got: Time: 14221099 Phase: 4 alt: 2977.187500

RSSI: -96

Got: Time: 14221270 Phase: 4 alt: 2958.812500

RSSI: -107

Got: Time: 14221441 Phase: 4 alt: 2961.562500

RSSI: -107

Got: Time: 14221609 Phase: 4 alt: 2959.625000

RSSI: -106

Got: Time: 14221779 Phase: 4 alt: 2947.562500

RSSI: -102

Got: Time: 14221948 Phase: 4 alt: 2947.687500

RSSI: -106

Got: Time: 14222286 Phase: 4 alt: 2935.625000

RSSI: -105

Got: Time: 14222454 Phase: 4 alt: 2926.375000

RSSI: -104

Got: Time: 14222625 Phase: 4 alt: 2921.312500

RSSI: -116

Got: Time: 14222796 Phase: 4 alt: 2921.875000

RSSI: -102

Got: Time: 14222964 Phase: 4 alt: 2927.312500

RSSI: -105

Got: Time: 14223474 Phase: 4 alt: 2899.500000

RSSI: -109

Got: Time: 14223645 Phase: 4 alt: 2903.062500

RSSI: -106

Got: Time: 14223814 Phase: 4 alt: 2897.000000

RSSI: -98

Got: Time: 14223984 Phase: 4 alt: 2894.625000

RSSI: -111

Got: Time: 14224322 Phase: 4 alt: 2883.000000

RSSI: -95

Got: Time: 14224490 Phase: 4 alt: 2883.812500

RSSI: -96

Got: Time: 14224659 Phase: 4 alt: 2882.437500

RSSI: -106

Got: Time: 14224829 Phase: 4 alt: 2878.125000

RSSI: -104

Got: Time: 14225000 Phase: 4 alt: 2873.875000

RSSI: -97

Got: Time: 14225168 Phase: 4 alt: 2866.812500

RSSI: -96

Got: Time: 14225339 Phase: 4 alt: 2867.687500

RSSI: -111

Got: Time: 14225508 Phase: 4 alt: 2853.875000

RSSI: -103

Got: Time: 14225679 Phase: 4 alt: 2850.187500

RSSI: -106

Got: Time: 14225849 Phase: 4 alt: 2853.250000

RSSI: -101

Got: Time: 14226018 Phase: 4 alt: 2845.500000

RSSI: -105

Got: Time: 14226189 Phase: 4 alt: 2840.187500

RSSI: -98

Got: Time: 14226357 Phase: 4 alt: 2829.937500

RSSI: -90

Got: Time: 14226527 Phase: 4 alt: 2823.687500

RSSI: -97

Got: Time: 14226696 Phase: 4 alt: 2828.437500

RSSI: -99

Got: Time: 14226864 Phase: 4 alt: 2825.000000

RSSI: -98

Got: Time: 14227034 Phase: 4 alt: 2825.875000

RSSI: -110

Got: Time: 14227372 Phase: 4 alt: 2813.625000

RSSI: -96

Got: Time: 14227543 Phase: 4 alt: 2806.875000

RSSI: -100

Got: Time: 14227712 Phase: 4 alt: 2804.625000

RSSI: -104

Got: Time: 14227883 Phase: 4 alt: 2804.000000

RSSI: -105

Got: Time: 14228053 Phase: 4 alt: 2802.625000

RSSI: -97

Got: Time: 14228222 Phase: 4 alt: 2794.125000

RSSI: -95

Got: Time: 14228393 Phase: 4 alt: 2783.500000

RSSI: -100

Got: Time: 14228562 Phase: 4 alt: 2787.375000

RSSI: -98

Got: Time: 14228731 Phase: 4 alt: 2782.062500

RSSI: -95

Got: Time: 14228900 Phase: 4 alt: 2774.750000

RSSI: -102

Got: Time: 14229068 Phase: 4 alt: 2765.625000

RSSI: -98

Got: Time: 14229577 Phase: 4 alt: 2757.437500

RSSI: -102

Got: Time: 14229747 Phase: 4 alt: 2750.625000

RSSI: -105

Got: Time: 14229916 Phase: 4 alt: 2744.187500

RSSI: -102

Got: Time: 14230087 Phase: 4 alt: 2734.625000

RSSI: -105

Got: Time: 14230258 Phase: 4 alt: 2735.750000

RSSI: -97

Got: Time: 14230426 Phase: 4 alt: 2733.937500

RSSI: -97

Got: Time: 14230597 Phase: 4 alt: 2733.062500

RSSI: -106

Got: Time: 14230766 Phase: 4 alt: 2727.562500

RSSI: -100

Got: Time: 14230936 Phase: 4 alt: 2716.750000

RSSI: -97

Got: Time: 14231105 Phase: 4 alt: 2710.062500

RSSI: -97

Got: Time: 14231273 Phase: 4 alt: 2701.312500

RSSI: -106

Got: Time: 14231442 Phase: 4 alt: 2701.375000

RSSI: -108

Got: Time: 14231612 Phase: 4 alt: 2704.312500

RSSI: -104

Got: Time: 14231781 Phase: 4 alt: 2705.312500

RSSI: -100

Got: Time: 14231951 Phase: 4 alt: 2699.812500

RSSI: -97

Got: Time: 14232120 Phase: 4 alt: 2689.062500

RSSI: -93

Got: Time: 14232291 Phase: 4 alt: 2685.062500

RSSI: -91

Got: Time: 14232462 Phase: 4 alt: 2675.500000

RSSI: -88

Got: Time: 14232630 Phase: 4 alt: 2667.437500

RSSI: -90

Got: Time: 14232801 Phase: 4 alt: 2669.687500

RSSI: -96

Got: Time: 14232970 Phase: 4 alt: 2673.250000

RSSI: -97

Got: Time: 14233140 Phase: 4 alt: 2668.750000

RSSI: -88

Got: Time: 14233310 Phase: 4 alt: 2655.875000

RSSI: -90

Got: Time: 14233478 Phase: 4 alt: 2654.062500

RSSI: -97

Got: Time: 14233647 Phase: 4 alt: 2645.375000

RSSI: -101

Got: Time: 14233816 Phase: 4 alt: 2649.250000

RSSI: -92

Got: Time: 14233985 Phase: 4 alt: 2638.062500

RSSI: -91

Got: Time: 14234156 Phase: 4 alt: 2628.062500

RSSI: -102

Got: Time: 14234324 Phase: 4 alt: 2620.250000

RSSI: -101

Got: Time: 14234495 Phase: 4 alt: 2624.312500

RSSI: -108

Got: Time: 14234666 Phase: 4 alt: 2624.937500

RSSI: -108

Got: Time: 14234835 Phase: 4 alt: 2622.750000

RSSI: -101

Got: Time: 14235005 Phase: 4 alt: 2610.437500

RSSI: -102

Got: Time: 14235174 Phase: 4 alt: 2602.312500

RSSI: -96

Got: Time: 14235345 Phase: 4 alt: 2602.187500

RSSI: -105

Got: Time: 14235515 Phase: 4 alt: 2606.687500

RSSI: -113

Got: Time: 14235684 Phase: 4 alt: 2597.875000

RSSI: -96

Got: Time: 14235853 Phase: 4 alt: 2589.312500

RSSI: -99

Got: Time: 14236022 Phase: 4 alt: 2579.250000

RSSI: -95

Got: Time: 14236191 Phase: 4 alt: 2581.875000

RSSI: -91

Got: Time: 14236360 Phase: 4 alt: 2584.000000

RSSI: -106

Got: Time: 14236529 Phase: 4 alt: 2573.187500

RSSI: -105

Got: Time: 14236700 Phase: 4 alt: 2566.875000

RSSI: -101

Got: Time: 14236871 Phase: 4 alt: 2562.375000

RSSI: -105

Got: Time: 14237039 Phase: 4 alt: 2555.875000

RSSI: -98

Got: Time: 14237210 Phase: 4 alt: 2554.625000

RSSI: -93

Got: Time: 14237379 Phase: 4 alt: 2542.812500

RSSI: -93

Got: Time: 14237549 Phase: 4 alt: 2541.500000

RSSI: -104

Got: Time: 14237720 Phase: 4 alt: 2548.187500

RSSI: -100

Got: Time: 14237889 Phase: 4 alt: 2540.500000

RSSI: -89

Got: Time: 14238059 Phase: 4 alt: 2533.562500

RSSI: -90

Got: Time: 14238228 Phase: 4 alt: 2526.187500

RSSI: -88

Got: Time: 14238397 Phase: 4 alt: 2529.125000

RSSI: -89

Got: Time: 14238566 Phase: 4 alt: 2524.625000

RSSI: -102

Got: Time: 14238734 Phase: 4 alt: 2518.375000

RSSI: -103

Got: Time: 14238904 Phase: 4 alt: 2515.062500

RSSI: -99

Got: Time: 14239075 Phase: 4 alt: 2510.625000

RSSI: -95

Got: Time: 14239244 Phase: 4 alt: 2496.937500

RSSI: -93

Got: Time: 14239415 Phase: 4 alt: 2495.187500

RSSI: -93

Got: Time: 14239583 Phase: 4 alt: 2489.437500

RSSI: -100

Got: Time: 14239754 Phase: 4 alt: 2488.125000

RSSI: -109

Got: Time: 14239925 Phase: 4 alt: 2486.312500

RSSI: -89

Got: Time: 14240264 Phase: 4 alt: 2477.250000

RSSI: -96

Got: Time: 14240433 Phase: 4 alt: 2478.437500

RSSI: -100

Got: Time: 14240602 Phase: 4 alt: 2472.500000

RSSI: -103

Got: Time: 14240771 Phase: 4 alt: 2471.937500

RSSI: -101

Got: Time: 14240940 Phase: 4 alt: 2462.125000

RSSI: -102

Got: Time: 14241109 Phase: 4 alt: 2454.187500

RSSI: -93

Got: Time: 14241279 Phase: 4 alt: 2450.187500

RSSI: -102

Got: Time: 14241449 Phase: 4 alt: 2443.562500

RSSI: -106

Got: Time: 14241619 Phase: 4 alt: 2445.437500

RSSI: -104

Got: Time: 14241788 Phase: 4 alt: 2446.250000

RSSI: -101

Got: Time: 14242129 Phase: 4 alt: 2431.750000

RSSI: -103

Got: Time: 14242298 Phase: 4 alt: 2425.625000

RSSI: -89

Got: Time: 14242469 Phase: 4 alt: 2416.812500

RSSI: -97

Got: Time: 14242637 Phase: 4 alt: 2426.187500

RSSI: -100

Got: Time: 14242808 Phase: 4 alt: 2427.250000

RSSI: -99

Got: Time: 14242978 Phase: 4 alt: 2420.312500

RSSI: -102

Got: Time: 14243315 Phase: 4 alt: 2403.312500

RSSI: -100

Got: Time: 14243484 Phase: 4 alt: 2397.000000

RSSI: -104

Got: Time: 14243653 Phase: 4 alt: 2396.375000

RSSI: -103

Got: Time: 14243823 Phase: 4 alt: 2395.500000

RSSI: -103

Got: Time: 14243992 Phase: 4 alt: 2391.937500

RSSI: -102

Got: Time: 14244163 Phase: 4 alt: 2382.625000

RSSI: -97

Got: Time: 14244334 Phase: 4 alt: 2381.250000

RSSI: -92

Got: Time: 14244502 Phase: 4 alt: 2371.125000

RSSI: -102

Got: Time: 14244673 Phase: 4 alt: 2370.375000

RSSI: -109

Got: Time: 14244842 Phase: 4 alt: 2379.500000

RSSI: -90

Got: Time: 14245013 Phase: 4 alt: 2369.187500

RSSI: -87

Got: Time: 14245352 Phase: 4 alt: 2357.375000

RSSI: -89

Got: Time: 14245522 Phase: 4 alt: 2348.437500

RSSI: -112

Got: Time: 14245691 Phase: 4 alt: 2350.312500

RSSI: -102

Got: Time: 14245860 Phase: 4 alt: 2349.062500

RSSI: -92

Got: Time: 14246028 Phase: 4 alt: 2338.937500

RSSI: -91

Got: Time: 14246197 Phase: 4 alt: 2344.750000

RSSI: -95

Got: Time: 14246368 Phase: 4 alt: 2344.187500

RSSI: -97

Got: Time: 14246538 Phase: 4 alt: 2339.812500

RSSI: -102

Got: Time: 14246707 Phase: 4 alt: 2318.125000

RSSI: -98

Got: Time: 14246878 Phase: 4 alt: 2321.750000

RSSI: -99

Got: Time: 14247046 Phase: 4 alt: 2324.437500

RSSI: -91

Got: Time: 14247217 Phase: 4 alt: 2319.687500

RSSI: -90

Got: Time: 14247557 Phase: 4 alt: 2303.750000

RSSI: -87

Got: Time: 14247727 Phase: 4 alt: 2301.312500

RSSI: -92

Got: Time: 14247896 Phase: 4 alt: 2302.812500

RSSI: -102

Got: Time: 14248065 Phase: 4 alt: 2297.250000

RSSI: -91

Got: Time: 14248234 Phase: 4 alt: 2302.812500

RSSI: -91

Got: Time: 14248403 Phase: 4 alt: 2297.937500

RSSI: -89

Got: Time: 14248572 Phase: 4 alt: 2285.312500

RSSI: -99

Got: Time: 14248742 Phase: 4 alt: 2276.500000

RSSI: -106

Got: Time: 14248911 Phase: 4 alt: 2276.625000

RSSI: -101

Got: Time: 14249082 Phase: 4 alt: 2279.500000

RSSI: -106

Got: Time: 14249421 Phase: 4 alt: 2269.812500

RSSI: -88

Got: Time: 14249592 Phase: 4 alt: 2273.125000

RSSI: -93

Got: Time: 14249761 Phase: 4 alt: 2265.375000

RSSI: -95

Got: Time: 14249932 Phase: 4 alt: 2259.437500

RSSI: -93

Got: Time: 14250100 Phase: 4 alt: 2261.437500

RSSI: -102

Got: Time: 14250270 Phase: 4 alt: 2253.312500

RSSI: -92

Got: Time: 14250438 Phase: 4 alt: 2253.562500

RSSI: -98

Got: Time: 14250607 Phase: 4 alt: 2248.875000

RSSI: -90

Got: Time: 14250776 Phase: 4 alt: 2237.062500

RSSI: -103

Got: Time: 14250947 Phase: 4 alt: 2231.312500

RSSI: -98

Got: Time: 14251116 Phase: 4 alt: 2224.562500

RSSI: -87

Got: Time: 14251286 Phase: 4 alt: 2229.312500

RSSI: -86

Got: Time: 14251455 Phase: 4 alt: 2229.062500

RSSI: -93

Got: Time: 14251626 Phase: 4 alt: 2219.062500

RSSI: -89

Got: Time: 14251796 Phase: 4 alt: 2215.812500

RSSI: -87

Got: Time: 14251965 Phase: 4 alt: 2205.437500

RSSI: -87

Got: Time: 14252136 Phase: 4 alt: 2201.062500

RSSI: -97

Got: Time: 14252305 Phase: 4 alt: 2197.500000

RSSI: -102

Got: Time: 14252475 Phase: 4 alt: 2191.562500

RSSI: -103

Got: Time: 14252644 Phase: 4 alt: 2196.375000

RSSI: -96

Got: Time: 14252813 Phase: 4 alt: 2192.937500

RSSI: -91

Got: Time: 14252981 Phase: 4 alt: 2187.062500

RSSI: -89

Got: Time: 14253151 Phase: 4 alt: 2186.687500

RSSI: -93

Got: Time: 14253320 Phase: 4 alt: 2175.000000

RSSI: -96

Got: Time: 14253491 Phase: 4 alt: 2180.750000

RSSI: -97

Got: Time: 14253659 Phase: 4 alt: 2170.250000

RSSI: -86

Got: Time: 14253830 Phase: 4 alt: 2169.562500

RSSI: -88

Got: Time: 14254001 Phase: 4 alt: 2164.500000

RSSI: -88

Got: Time: 14254170 Phase: 4 alt: 2160.437500

RSSI: -87

Got: Time: 14254340 Phase: 4 alt: 2152.812500

RSSI: -88

Got: Time: 14254509 Phase: 4 alt: 2158.750000

RSSI: -90

Got: Time: 14254680 Phase: 4 alt: 2155.312500

RSSI: -89

Got: Time: 14254851 Phase: 4 alt: 2145.187500

RSSI: -90

Got: Time: 14255019 Phase: 4 alt: 2139.625000

RSSI: -90

Got: Time: 14255189 Phase: 4 alt: 2132.875000

RSSI: -89

Got: Time: 14255358 Phase: 4 alt: 2129.750000

RSSI: -90

Got: Time: 14255527 Phase: 4 alt: 2134.000000

RSSI: -90

Got: Time: 14255696 Phase: 4 alt: 2136.062500

RSSI: -89

Got: Time: 14255864 Phase: 4 alt: 2132.312500

RSSI: -101

Got: Time: 14256035 Phase: 4 alt: 2122.437500

RSSI: -91

Got: Time: 14256205 Phase: 4 alt: 2120.937500

RSSI: -82

Got: Time: 14256375 Phase: 4 alt: 2102.687500

RSSI: -88

Got: Time: 14256545 Phase: 4 alt: 2110.875000

RSSI: -91

Got: Time: 14256714 Phase: 4 alt: 2110.312500

RSSI: -92

Got: Time: 14256885 Phase: 4 alt: 2095.187500

RSSI: -104

Got: Time: 14257056 Phase: 4 alt: 2090.312500

RSSI: -86

Got: Time: 14257224 Phase: 4 alt: 2084.500000

RSSI: -83

Got: Time: 14257395 Phase: 4 alt: 2084.312500

RSSI: -90

Got: Time: 14257564 Phase: 4 alt: 2085.437500

RSSI: -95

Got: Time: 14257734 Phase: 4 alt: 2086.500000

RSSI: -98

Got: Time: 14257903 Phase: 4 alt: 2082.937500

RSSI: -103

Got: Time: 14258072 Phase: 4 alt: 2068.875000

RSSI: -99

Got: Time: 14258240 Phase: 4 alt: 2062.062500

RSSI: -91

Got: Time: 14258410 Phase: 4 alt: 2064.687500

RSSI: -98

Got: Time: 14258580 Phase: 4 alt: 2062.187500

RSSI: -90

Got: Time: 14258750 Phase: 4 alt: 2056.562500

RSSI: -89

Got: Time: 14258919 Phase: 4 alt: 2052.687500

RSSI: -96

Got: Time: 14259089 Phase: 4 alt: 2044.687500

RSSI: -103

Got: Time: 14259260 Phase: 4 alt: 2047.875000

RSSI: -88

Got: Time: 14259429 Phase: 4 alt: 2044.750000

RSSI: -96

Got: Time: 14259600 Phase: 4 alt: 2033.125000

RSSI: -91

Got: Time: 14259768 Phase: 4 alt: 2028.000000

RSSI: -101

Got: Time: 14259939 Phase: 4 alt: 2027.375000

RSSI: -92

Got: Time: 14260110 Phase: 4 alt: 2037.437500

RSSI: -96

Got: Time: 14260279 Phase: 4 alt: 2029.750000

RSSI: -113

Got: Time: 14260449 Phase: 4 alt: 2020.500000

RSSI: -102

Got: Time: 14260617 Phase: 4 alt: 2015.812500

RSSI: -100

Got: Time: 14260786 Phase: 4 alt: 2012.125000

RSSI: -92

Got: Time: 14260955 Phase: 4 alt: 2011.687500

RSSI: -92

Got: Time: 14261124 Phase: 4 alt: 2001.812500

RSSI: -92

Got: Time: 14261294 Phase: 4 alt: 1990.750000

RSSI: -100

Got: Time: 14261465 Phase: 4 alt: 2005.625000

RSSI: -101

Got: Time: 14261633 Phase: 4 alt: 2000.125000

RSSI: -98

Got: Time: 14261804 Phase: 4 alt: 1995.750000

RSSI: -95

Got: Time: 14261973 Phase: 4 alt: 1993.375000

RSSI: -95

Got: Time: 14262144 Phase: 4 alt: 1987.937500

RSSI: -92

Got: Time: 14262314 Phase: 4 alt: 1985.812500

RSSI: -99

Got: Time: 14262483 Phase: 4 alt: 1980.062500

RSSI: -96

Got: Time: 14262654 Phase: 4 alt: 1973.250000

RSSI: -89

Got: Time: 14262822 Phase: 4 alt: 1968.750000

RSSI: -88

Got: Time: 14262992 Phase: 4 alt: 1965.187500

RSSI: -87

Got: Time: 14263160 Phase: 4 alt: 1963.750000

RSSI: -91

Got: Time: 14263329 Phase: 4 alt: 1958.125000

RSSI: -83

Got: Time: 14263499 Phase: 4 alt: 1946.125000

RSSI: -84

Got: Time: 14263669 Phase: 4 alt: 1951.187500

RSSI: -84

Got: Time: 14263838 Phase: 4 alt: 1948.500000

RSSI: -95

Got: Time: 14264009 Phase: 4 alt: 1936.937500

RSSI: -88

Got: Time: 14264177 Phase: 4 alt: 1928.375000

RSSI: -81

Got: Time: 14264348 Phase: 4 alt: 1921.625000

RSSI: -84

Got: Time: 14264519 Phase: 4 alt: 1925.000000

RSSI: -89

Got: Time: 14264688 Phase: 4 alt: 1927.437500

RSSI: -91

Got: Time: 14264858 Phase: 4 alt: 1921.687500

RSSI: -89

Got: Time: 14265027 Phase: 4 alt: 1914.812500

RSSI: -84

Got: Time: 14265197 Phase: 4 alt: 1905.500000

RSSI: -88

Got: Time: 14265366 Phase: 4 alt: 1904.187500

RSSI: -88

Got: Time: 14265535 Phase: 4 alt: 1902.625000

RSSI: -100

Got: Time: 14265704 Phase: 4 alt: 1897.875000

RSSI: -89

Got: Time: 14265873 Phase: 4 alt: 1893.500000

RSSI: -98

Got: Time: 14266042 Phase: 4 alt: 1890.437500

RSSI: -104

Got: Time: 14266213 Phase: 4 alt: 1886.375000

RSSI: -99

Got: Time: 14266381 Phase: 4 alt: 1884.062500

RSSI: -88

Got: Time: 14266552 Phase: 4 alt: 1878.562500

RSSI: -92

Got: Time: 14266723 Phase: 4 alt: 1870.187500

RSSI: -84

Got: Time: 14266892 Phase: 4 alt: 1870.687500

RSSI: -86

Got: Time: 14267062 Phase: 4 alt: 1873.937500

RSSI: -96

Got: Time: 14267231 Phase: 4 alt: 1871.125000

RSSI: -91

Got: Time: 14267401 Phase: 4 alt: 1862.937500

RSSI: -96

Got: Time: 14267572 Phase: 4 alt: 1863.562500

RSSI: -89

Got: Time: 14267741 Phase: 4 alt: 1865.687500

RSSI: -87

Got: Time: 14267909 Phase: 4 alt: 1848.000000

RSSI: -96

Got: Time: 14268078 Phase: 4 alt: 1842.125000

RSSI: -90

Got: Time: 14268247 Phase: 4 alt: 1848.437500

RSSI: -103

Got: Time: 14268417 Phase: 4 alt: 1842.875000

RSSI: -92

Got: Time: 14268586 Phase: 4 alt: 1829.312500

RSSI: -91

Got: Time: 14268756 Phase: 4 alt: 1837.812500

RSSI: -103

Got: Time: 14268927 Phase: 4 alt: 1824.312500

RSSI: -101

Got: Time: 14269096 Phase: 4 alt: 1821.250000

RSSI: -81

Got: Time: 14269267 Phase: 4 alt: 1810.562500

RSSI: -93

Got: Time: 14269436 Phase: 4 alt: 1812.562500

RSSI: -85

Got: Time: 14269606 Phase: 4 alt: 1812.312500

RSSI: -83

Got: Time: 14269777 Phase: 4 alt: 1801.250000

RSSI: -96

Got: Time: 14269946 Phase: 4 alt: 1799.437500

RSSI: -95

Got: Time: 14270116 Phase: 4 alt: 1796.750000

RSSI: -97

Got: Time: 14270284 Phase: 4 alt: 1790.625000

RSSI: -103

Got: Time: 14270453 Phase: 4 alt: 1786.250000

RSSI: -95

Got: Time: 14270622 Phase: 4 alt: 1789.062500

RSSI: -100

Got: Time: 14270791 Phase: 4 alt: 1784.500000

RSSI: -98

Got: Time: 14270961 Phase: 4 alt: 1778.375000

RSSI: -97

Got: Time: 14271132 Phase: 4 alt: 1773.125000

RSSI: -97

Got: Time: 14271300 Phase: 4 alt: 1766.937500

RSSI: -101

Got: Time: 14271471 Phase: 4 alt: 1764.562500

RSSI: -91

Got: Time: 14271640 Phase: 4 alt: 1760.750000

RSSI: -97

Got: Time: 14271811 Phase: 4 alt: 1764.437500

RSSI: -98

Got: Time: 14271981 Phase: 4 alt: 1763.687500

RSSI: -102

Got: Time: 14272150 Phase: 4 alt: 1757.875000

RSSI: -95

Got: Time: 14272321 Phase: 4 alt: 1755.500000

RSSI: -101

Got: Time: 14272489 Phase: 4 alt: 1749.750000

RSSI: -97

Got: Time: 14272658 Phase: 4 alt: 1744.937500

RSSI: -88

Got: Time: 14272827 Phase: 4 alt: 1739.375000

RSSI: -88

Got: Time: 14272827 Phase: 5 alt: 1712.500000

RSSI: -87

Got: Time: 14274208 Phase: 5 alt: 1702.687500

RSSI: -85

Got: Time: 14274377 Phase: 5 alt: 1697.437500

RSSI: -83

Got: Time: 14274545 Phase: 5 alt: 1695.437500

RSSI: -85

Got: Time: 14274714 Phase: 5 alt: 1692.562500

RSSI: -87

Got: Time: 14274884 Phase: 5 alt: 1690.687500

RSSI: -88

Got: Time: 14275054 Phase: 5 alt: 1681.000000

RSSI: -89

Got: Time: 14275223 Phase: 5 alt: 1684.000000

RSSI: -86

Got: Time: 14275394 Phase: 5 alt: 1685.750000

RSSI: -85

Got: Time: 14275563 Phase: 5 alt: 1680.062500

RSSI: -83

Got: Time: 14275733 Phase: 5 alt: 1674.625000

RSSI: -91

Got: Time: 14275904 Phase: 5 alt: 1667.437500

RSSI: -100

Got: Time: 14276073 Phase: 5 alt: 1662.875000

RSSI: -89

Got: Time: 14276243 Phase: 5 alt: 1658.000000

RSSI: -87

Got: Time: 14276412 Phase: 5 alt: 1651.125000

RSSI: -96

Got: Time: 14276582 Phase: 5 alt: 1651.000000

RSSI: -93

Got: Time: 14276750 Phase: 5 alt: 1648.875000

RSSI: -87

Got: Time: 14276919 Phase: 5 alt: 1643.250000

RSSI: -86

Got: Time: 14277088 Phase: 5 alt: 1641.125000

RSSI: -87

Got: Time: 14277259 Phase: 5 alt: 1639.812500

RSSI: -82

Got: Time: 14277427 Phase: 5 alt: 1626.125000

RSSI: -84

Got: Time: 14277598 Phase: 5 alt: 1625.250000

RSSI: -87

Got: Time: 14277767 Phase: 5 alt: 1625.562500

RSSI: -81

Got: Time: 14277938 Phase: 5 alt: 1620.625000

RSSI: -89

Got: Time: 14278108 Phase: 5 alt: 1619.000000

RSSI: -85

Got: Time: 14278277 Phase: 5 alt: 1615.312500

RSSI: -95

Got: Time: 14278448 Phase: 5 alt: 1607.000000

RSSI: -101

Got: Time: 14278616 Phase: 5 alt: 1601.812500

RSSI: -85

Got: Time: 14278786 Phase: 5 alt: 1602.750000

RSSI: -85

Got: Time: 14278955 Phase: 5 alt: 1603.687500

RSSI: -84

Got: Time: 14279124 Phase: 5 alt: 1603.750000

RSSI: -92

Got: Time: 14279293 Phase: 5 alt: 1591.500000

RSSI: -86

Got: Time: 14279463 Phase: 5 alt: 1452.812500

RSSI: -93

Got: Time: 14279632 Phase: 5 alt: 1567.812500

RSSI: -96

Got: Time: 14279803 Phase: 5 alt: 1590.750000

RSSI: -97

Got: Time: 14279971 Phase: 5 alt: 1584.562500

RSSI: -91

Got: Time: 14280142 Phase: 5 alt: 1582.187500

RSSI: -92

Got: Time: 14280313 Phase: 5 alt: 1567.937500

RSSI: -91

Got: Time: 14280481 Phase: 5 alt: 1567.312500

RSSI: -96

Got: Time: 14280652 Phase: 5 alt: 1562.875000

RSSI: -113

Got: Time: 14280821 Phase: 5 alt: 1559.187500

RSSI: -90

Got: Time: 14280991 Phase: 5 alt: 1564.375000

RSSI: -92

Got: Time: 14281161 Phase: 5 alt: 1552.062500

RSSI: -79

Got: Time: 14281330 Phase: 5 alt: 1542.937500

RSSI: -80

Got: Time: 14281498 Phase: 5 alt: 1543.000000

RSSI: -88

Got: Time: 14281667 Phase: 5 alt: 1545.000000

RSSI: -86

Got: Time: 14281837 Phase: 5 alt: 1543.500000

RSSI: -109

Got: Time: 14282007 Phase: 5 alt: 1544.062500

RSSI: -88

Got: Time: 14282176 Phase: 5 alt: 1525.687500

RSSI: -87

Got: Time: 14282346 Phase: 5 alt: 1521.250000

RSSI: -89

Got: Time: 14282517 Phase: 5 alt: 1522.750000

RSSI: -95

Got: Time: 14282686 Phase: 5 alt: 1519.000000

RSSI: -85

Got: Time: 14282857 Phase: 5 alt: 1510.812500

RSSI: -96

Got: Time: 14283025 Phase: 5 alt: 1508.875000

RSSI: -83

Got: Time: 14283196 Phase: 5 alt: 1501.625000

RSSI: -81

Got: Time: 14283367 Phase: 5 alt: 1496.687500

RSSI: -92

Got: Time: 14283536 Phase: 5 alt: 1493.812500

RSSI: -90

Got: Time: 14283706 Phase: 5 alt: 1488.000000

RSSI: -85

Got: Time: 14283874 Phase: 5 alt: 1492.687500

RSSI: -99

Got: Time: 14284043 Phase: 5 alt: 1489.625000

RSSI: -87

Got: Time: 14284212 Phase: 5 alt: 1482.000000

RSSI: -87

Got: Time: 14284381 Phase: 5 alt: 1477.750000

RSSI: -90

Got: Time: 14284551 Phase: 5 alt: 1470.687500

RSSI: -89

Got: Time: 14284722 Phase: 5 alt: 1463.750000

RSSI: -87

Got: Time: 14284891 Phase: 5 alt: 1463.625000

RSSI: -90

Got: Time: 14285062 Phase: 5 alt: 1463.875000

RSSI: -87

Got: Time: 14285230 Phase: 5 alt: 1458.250000

RSSI: -90

Got: Time: 14285401 Phase: 5 alt: 1457.250000

RSSI: -95

Got: Time: 14285572 Phase: 5 alt: 1454.437500

RSSI: -84

Got: Time: 14285741 Phase: 5 alt: 1449.687500

RSSI: -83

Got: Time: 14285911 Phase: 5 alt: 1449.312500

RSSI: -92

Got: Time: 14286080 Phase: 5 alt: 1447.375000

RSSI: -88

Got: Time: 14286250 Phase: 5 alt: 1435.312500

RSSI: -86

Got: Time: 14286419 Phase: 5 alt: 1439.125000

RSSI: -93

Got: Time: 14286588 Phase: 5 alt: 1432.687500

RSSI: -85

Got: Time: 14286757 Phase: 5 alt: 1420.812500

RSSI: -90

Got: Time: 14286926 Phase: 5 alt: 1419.437500

RSSI: -92

Got: Time: 14287096 Phase: 5 alt: 1417.875000

RSSI: -98

Got: Time: 14287435 Phase: 5 alt: 1411.937500

RSSI: -88

Got: Time: 14287606 Phase: 5 alt: 1406.125000

RSSI: -87

Got: Time: 14287777 Phase: 5 alt: 1405.437500

RSSI: -86

Got: Time: 14287946 Phase: 5 alt: 1395.562500

RSSI: -92

Got: Time: 14288116 Phase: 5 alt: 1389.000000

RSSI: -89

Got: Time: 14288285 Phase: 5 alt: 1388.250000

RSSI: -91

Got: Time: 14288456 Phase: 5 alt: 1388.187500

RSSI: -87

Got: Time: 14288627 Phase: 5 alt: 1387.875000

RSSI: -85

Got: Time: 14288795 Phase: 5 alt: 1381.187500

RSSI: -90

Got: Time: 14288965 Phase: 5 alt: 1374.687500

RSSI: -88

Got: Time: 14289134 Phase: 5 alt: 1366.500000

RSSI: -82

Got: Time: 14289303 Phase: 5 alt: 1366.875000

RSSI: -83

Got: Time: 14289472 Phase: 5 alt: 1363.312500

RSSI: -87

Got: Time: 14289640 Phase: 5 alt: 1362.125000

RSSI: -88

Got: Time: 14289811 Phase: 5 alt: 1356.562500

RSSI: -89

Got: Time: 14289981 Phase: 5 alt: 1352.187500

RSSI: -85

Got: Time: 14290150 Phase: 5 alt: 1350.375000

RSSI: -89

Got: Time: 14290321 Phase: 5 alt: 1347.437500

RSSI: -83

Got: Time: 14290490 Phase: 5 alt: 1342.312500

RSSI: -82

Got: Time: 14290660 Phase: 5 alt: 1339.812500

RSSI: -79

Got: Time: 14290831 Phase: 5 alt: 1332.125000

RSSI: -91

Got: Time: 14291000 Phase: 5 alt: 1327.125000

RSSI: -97

Got: Time: 14291170 Phase: 5 alt: 1320.250000

RSSI: -89

Got: Time: 14291339 Phase: 5 alt: 1315.437500

RSSI: -80

Got: Time: 14291508 Phase: 5 alt: 1315.000000

RSSI: -81

Got: Time: 14291677 Phase: 5 alt: 1308.125000

RSSI: -83

Got: Time: 14291846 Phase: 5 alt: 1304.875000

RSSI: -91

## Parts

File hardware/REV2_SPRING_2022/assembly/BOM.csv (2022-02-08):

Comment | Designator | Footprint | LCSC Part #
C_0.1u | C101, C201, C202, C203, C301, C302, C303, | 0805 | C28233
LED | D101, D102, D103, D104, D105, D106, | 0805 | C2296
R_15k | R101, | 0805 | C17475
R_4.7k | R102, | 0805 | C17673
R_10k | R103, R109, R110, R111, R112, R114, R115, R202, R302, | 0805 | C17414
R_750 | R104, R105, R106, R107, R108, R113, | 0805 | C17818
R_200 | R201, R203, R301, R303, | 0805 | C17540

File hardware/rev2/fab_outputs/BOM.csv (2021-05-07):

Comment | Designator | Footprint | LCSC Part # | LCSC Part Type
Conn_02x03_Odd_Even | J3 | Molex_Nano-Fit_105312-1106
LED | D2,D3,D4,D5,D6,D7 | AA3528LSECKT-J4
PKB24SPCH3601-B0 | LS1 | PT-1340
100n | C7,C9,C10 | C_0805_OEM
10u | C8 | C_0805_OEM
R_4.99K | R1,R2 | R_0805_OEM
MPL3115A2 | U2 | MPL3115A2
Teensy3.6 | U3 | Teensy3-6
1u | C11 | C_0805_OEM
ADXL345BCCZ | U5 | ADXL345
RFM9X_header | J2 | RFM9X_header
Conn_01x09_Female | J1 | PinSocket_1x09_P2.54mm_Vertical
R_20k | R5 | R_0805_OEM
C_1uF | C14 | C_0805_OEM
R_8k | R6 | R_0805_OEM
R_475 | R7 | R_0805_OEM
TPS2113ADRBR | U7 | TPS2113ADRBR
C_10uF | C1 | C_0805_OEM
D_Zener | D1 | SOT-23
R_20 | R3 | R_0805_OEM
R_750 | R4,R8,R9,R10,R11,R12 | R_0805_OEM

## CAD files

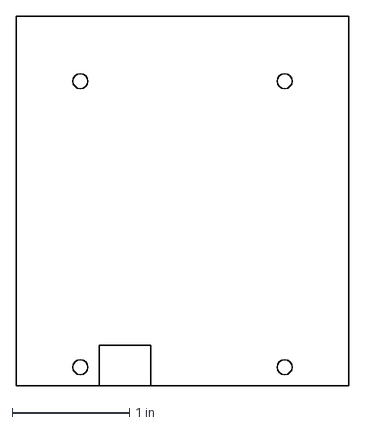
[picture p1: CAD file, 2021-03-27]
hardware/rev2/MainFlightComputer.dxf
2.83 x 3.15 in

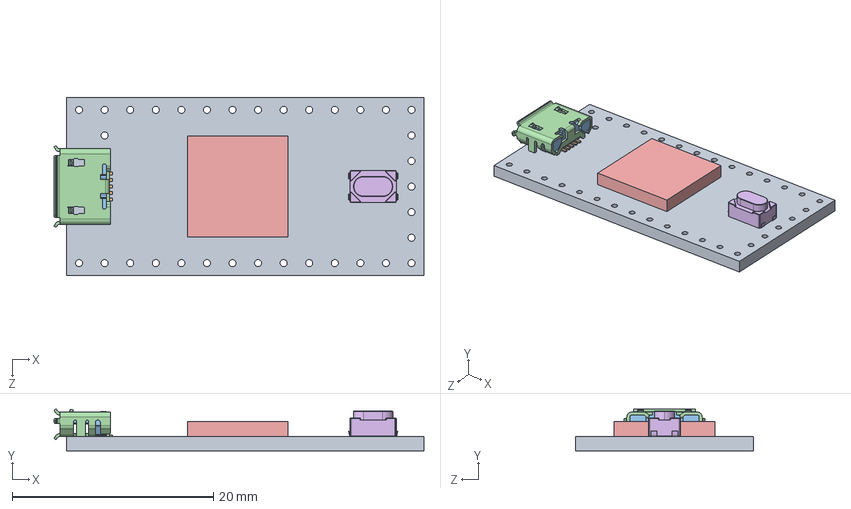
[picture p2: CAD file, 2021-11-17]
kicad_symbol_libraries/teensy.pretty-master/Teensy_4.0_Assembly.STEP
36.8 x 4.12 x 17.7 mm
Teensy_4.0_PCB
Micro USB-B Female 5Pin SMD
NXP iMXRT1062
SKRPACE010 v4

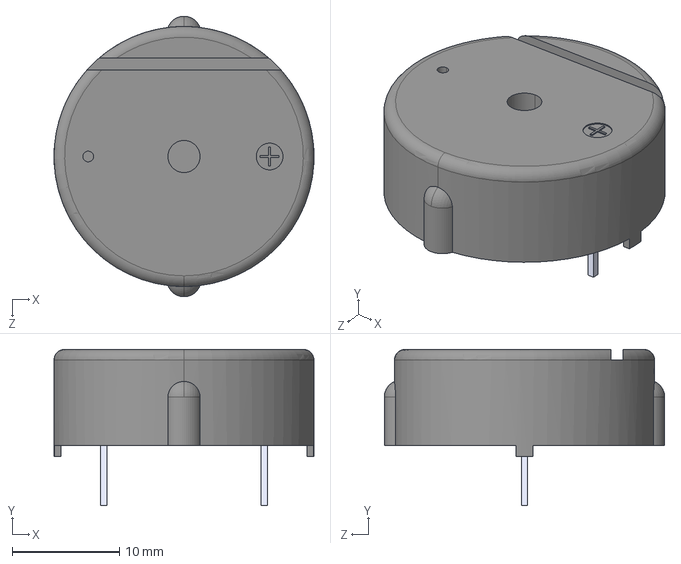
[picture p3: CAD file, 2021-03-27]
hardware/libraries-symbols/rev2_lib/PKB24SPCH3601-B0.step
24.3 x 14.6 x 26.2 mm

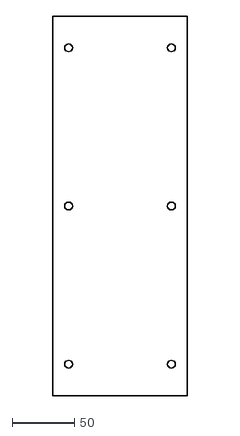
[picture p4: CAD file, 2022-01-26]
hardware/REV1_FALL_2021/Rev_2_Rectangular_Board_Shape.dxf
108.0 x 304.8

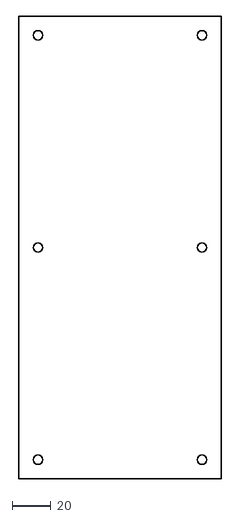
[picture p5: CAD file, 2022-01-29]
hardware/REV2_SPRING_2022/Rev_2_Rectangular_Board_Shape3.dxf
105.0 x 240.0

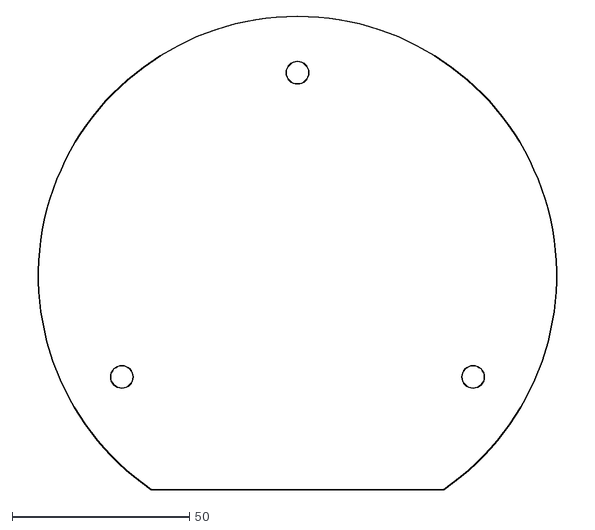
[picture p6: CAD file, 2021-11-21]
hardware/REV1_FALL_2021/Rev_1_Circuilar_Board_Shape1.dxf
158.4 x 133.4

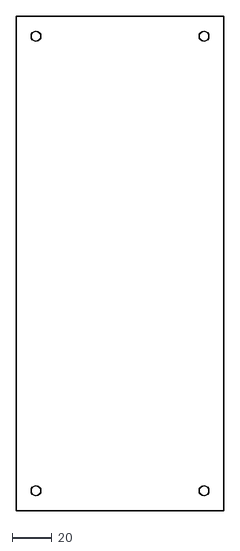
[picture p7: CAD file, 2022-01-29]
hardware/REV2_SPRING_2022/Rev_2_Rectangular_Board_Shape4.dxf
105.0 x 250.0

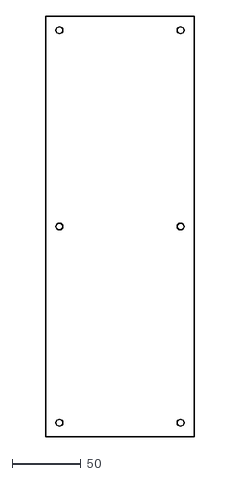
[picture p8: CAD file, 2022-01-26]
hardware/REV2_SPRING_2022/Rev_2_Rectangular_Board_Shape2.dxf
108.0 x 304.8

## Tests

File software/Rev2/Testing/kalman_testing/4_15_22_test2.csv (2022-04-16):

Time since launch (ms) | X Acceleration (m/s) | Y Acceleration (m/s) | Z Acceleration (m/s) | X Orientation | Y Orientation | Z Orientation | Global Z Accel | Altitude (m) | Latitude | Longitude | Phase | Kalman Altitude | Global Z Vel | Kalman Global Z Accel
3679 | -0.30000001192092896 | -0.009999999776482582 | -0.0 | 0.3125 | 271.125 | 360.0 | -0.2999432682991028 | 57.625 | 3.0 | 3.0 | 3 | 57.625 | 10.0 | -0.2999432682991028
4203 | -0.30000001192092896 | -0.009999999776482582 | -0.0 | 0.3125 | 271.125 | 360.0 | -0.2999432682991028 | 57.875 | 3.0 | 3.0 | 3 | -0.31254586577415466 | 0.0 | 0.0
4726 | -0.3100000023841858 | -0.0 | -0.0 | 0.3125 | 271.125 | 360.0 | -0.30994027853012085 | 57.625 | 3.0 | 3.0 | 3 | -0.34453269839286804 | 0.0 | 0.0
5250 | -0.3199999928474426 | -0.0 | -0.0 | 0.3125 | 271.125 | 360.0 | -0.3199383318424225 | 57.875 | 3.0 | 3.0 | 3 | -0.3642825186252594 | 0.0 | 0.0
5774 | -0.3199999928474426 | -0.0 | -0.019999999552965164 | 0.3125 | 271.125 | 360.0 | -0.3203309178352356 | 57.875 | 3.0 | 3.0 | 3 | -0.3653147518634796 | 0.0 | 0.0
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

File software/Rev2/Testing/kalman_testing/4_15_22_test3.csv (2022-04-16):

Time since launch (ms) | X Acceleration (m/s) | Y Acceleration (m/s) | Z Acceleration (m/s) | X Orientation | Y Orientation | Z Orientation | Global Z Accel | Altitude (m) | Latitude | Longitude | Phase | Kalman Altitude | Global Z Vel | Kalman Global Z Accel
2809 | -0.28999999165534973 | 0.009999999776482582 | -0.0 | 0.3125 | 271.5625 | 0.125 | -0.28989070653915405 | 58.6875 | 3.0 | 3.0 | 3 | 58.6875 | 10.0 | -0.28989070653915405
3333 | -0.3100000023841858 | -0.0 | -0.009999999776482582 | 0.3125 | 271.5625 | 0.125 | -0.3101573884487152 | 59.3125 | 3.0 | 3.0 | 3 | 61.433902740478516 | 9.611441612243652 | -0.31370043754577637
3856 | -0.33000001311302185 | 0.029999999329447746 | -0.029999999329447746 | 0.3125 | 271.5625 | 0.125 | -0.33069077134132385 | 59.1875 | 3.0 | 3.0 | 3 | 62.008514404296875 | 8.352315902709961 | -0.3564586937427521
4380 | -0.33000001311302185 | -0.0 | -0.0 | 0.3125 | 271.5625 | 0.125 | -0.3298773467540741 | 59.1875 | 3.0 | 3.0 | 3 | 61.69854736328125 | 6.434121608734131 | -0.3758251667022705
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

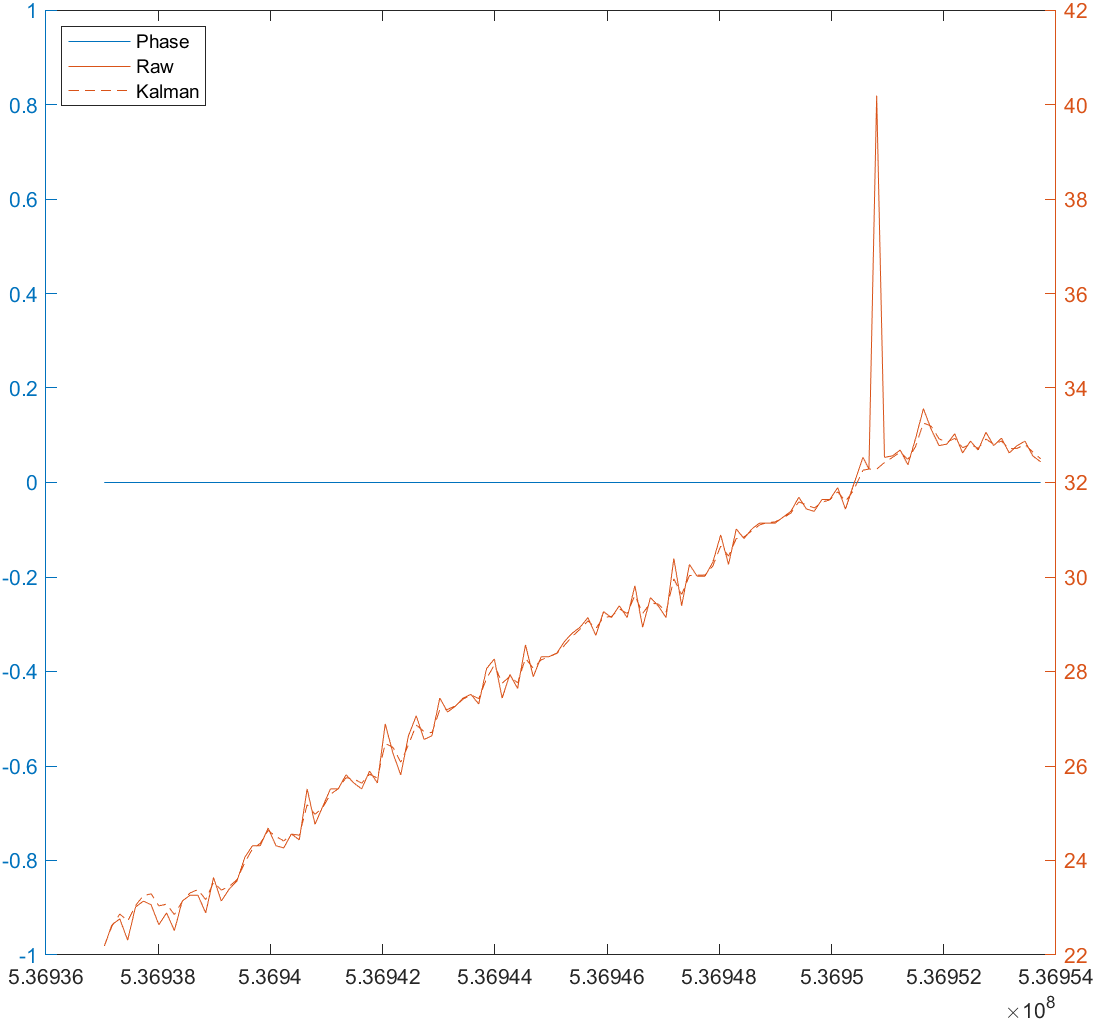
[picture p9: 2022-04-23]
software/Rev2/Testing/kalman_testing/untitled1.png

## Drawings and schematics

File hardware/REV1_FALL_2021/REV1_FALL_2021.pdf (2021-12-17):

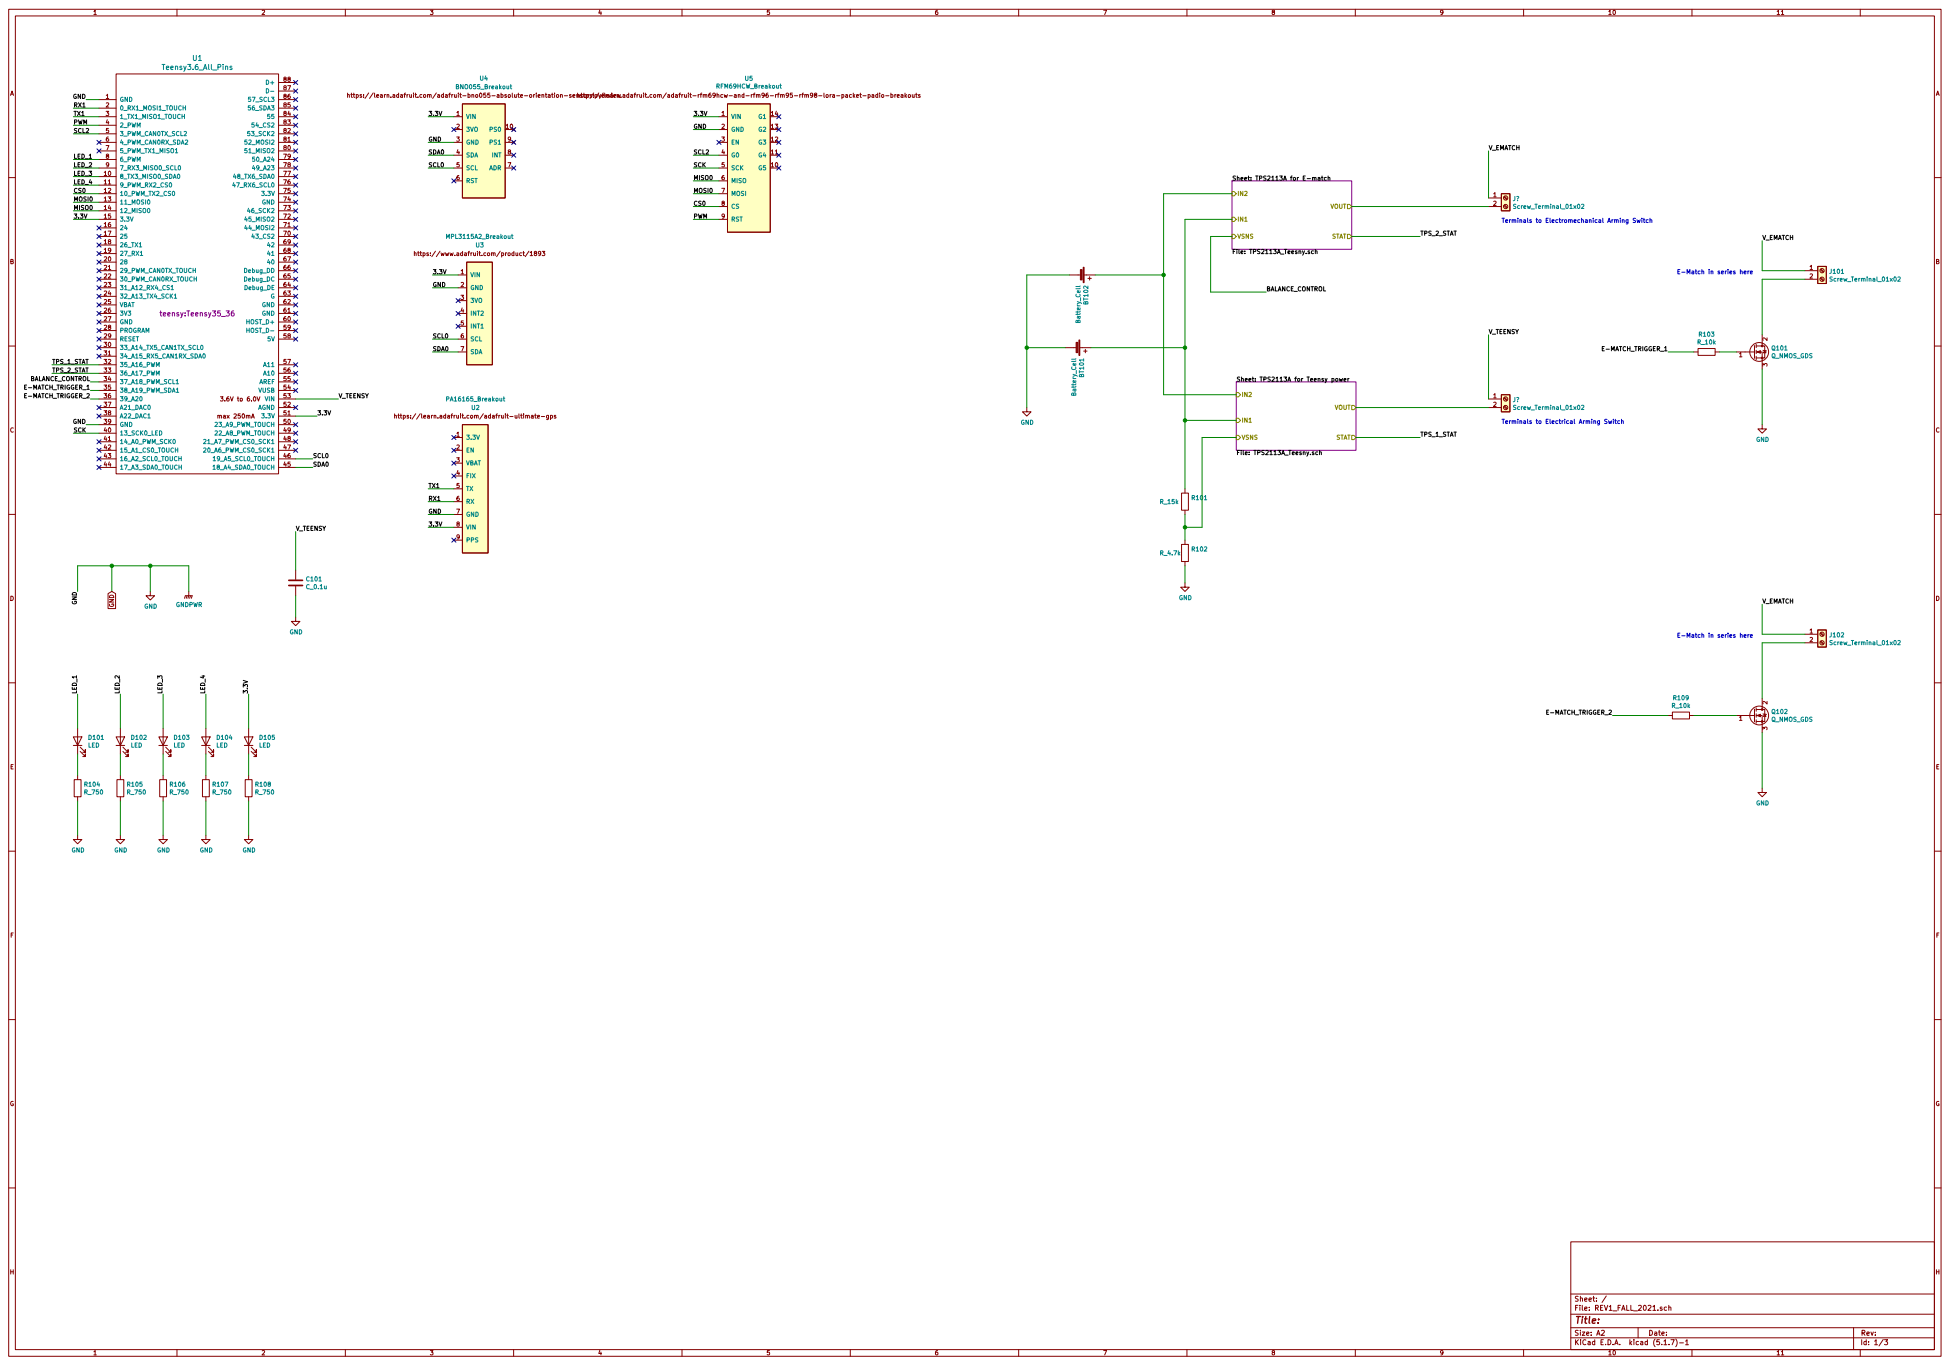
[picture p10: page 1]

https://learn.adafruit.com/adafruit-bno055-absolute-orientation-sensor/overview

Sheet: TPS2113A for E-match File: TPS2113A_Teesny.sch

Terminals to Electromechanical Arming Switch

Sheet: TPS2113A for Teensy power

Terminals to Electrical Arming Switch

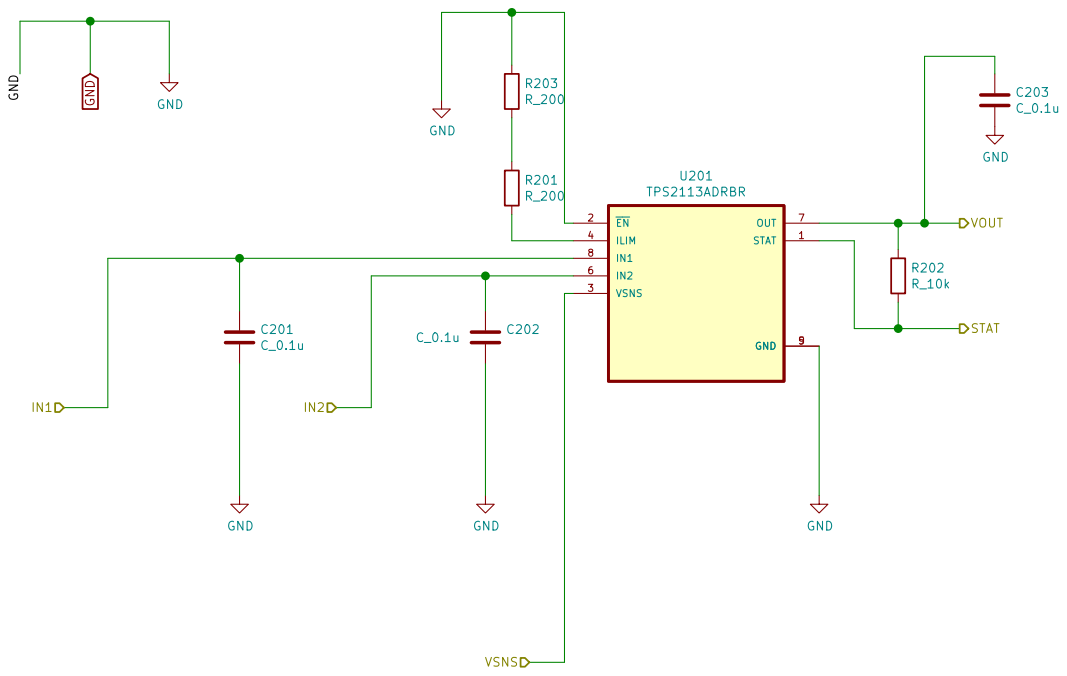
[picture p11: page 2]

VOUT STAT GND GND

File: TPS2113A_Teesny.sch Sheet: /TPS2113A for E-match/
Id: 2/3 Title:

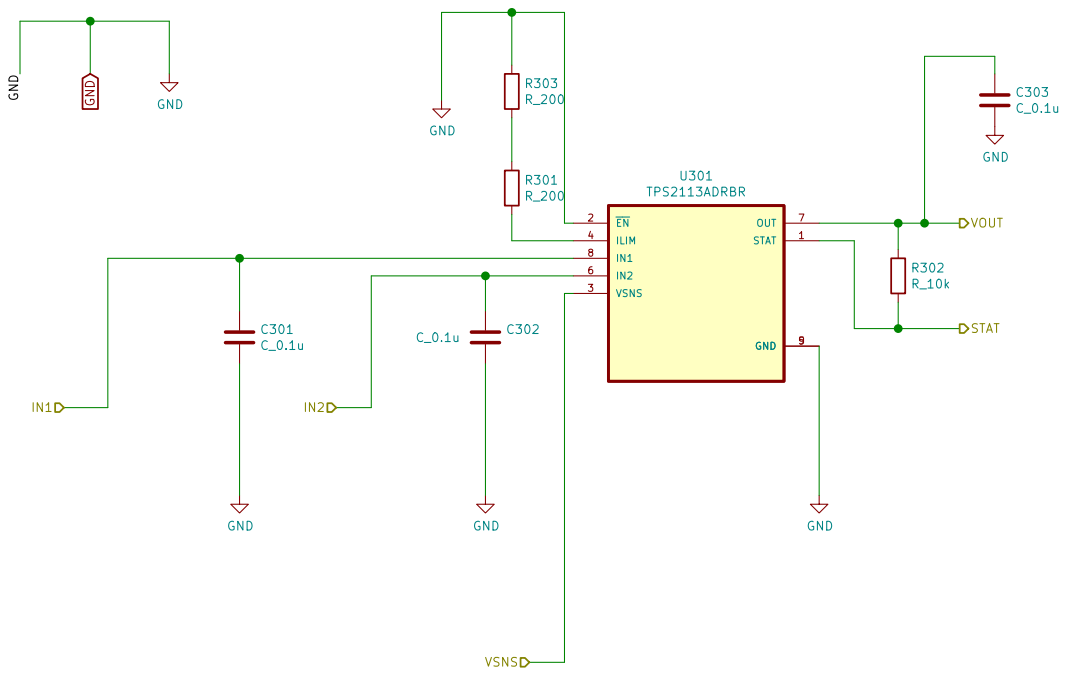
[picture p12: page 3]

VOUT STAT GND GND

Sheet: /TPS2113A for Teensy power/
File: TPS2113A_Teesny.sch
Id: 3/3 Title:

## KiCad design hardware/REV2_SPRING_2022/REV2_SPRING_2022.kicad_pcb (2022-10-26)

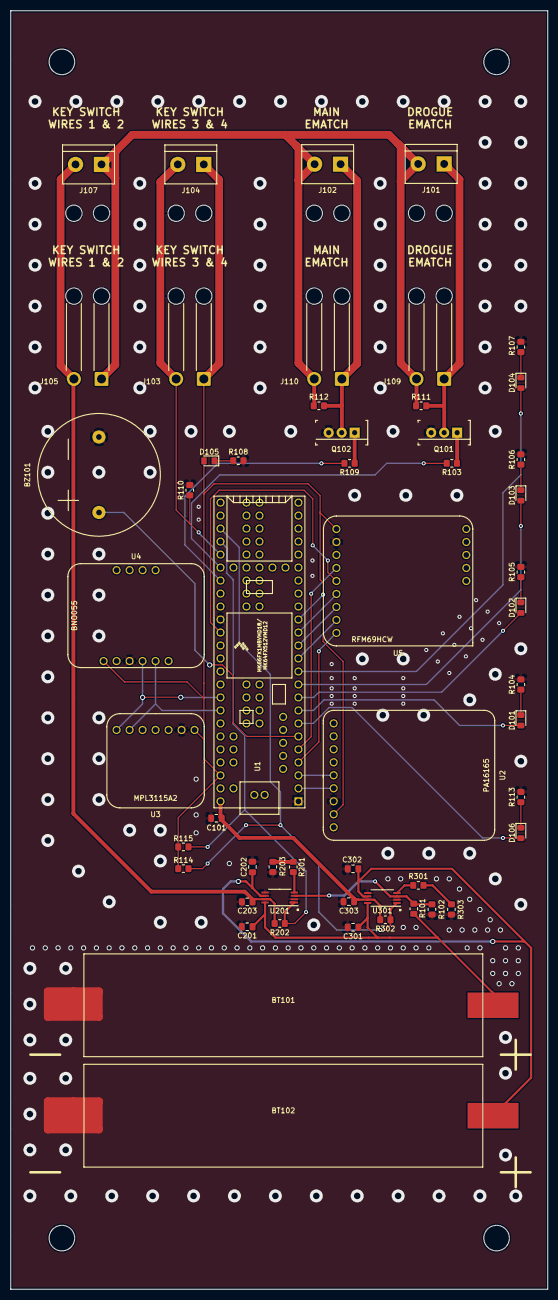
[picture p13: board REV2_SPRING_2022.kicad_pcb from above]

Board: 2 copper layers, 105.0 x 250.0 mm, 54 parts (0 on the bottom side), 43 nets.

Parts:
BT101, BT102: Battery_Cell; MyBatteryHolder_MPD_BH-18650-PC2
BZ101: Buzzer; Large_Buzzer_24mmOD_14.8mmPinDistance_1.0mmPinDiameter
C101, C201, C202, C203, C301, C302, C303: C_0.1u; C_0805_2012Metric_Pad1.18x1.45mm_HandSolder
D101, D102, D103, D104, D105, D106: LED; LED_0805_2012Metric_Pad1.15x1.40mm_HandSolder
J101, J102, J104, J107: Screw_Terminal_01x02; TerminalBlock_bornier-2_P5.08mm
J103, J105, J109, J110: Conn_01x02_Female; SolderWire-1sqmm_1x02_P5.4mm_D1.4mm_OD2.7mm_Relief2x
Q101, Q102: Q_NMOS_GDS; TO-220-3
R101: R_15k; R_0805_2012Metric_Pad1.20x1.40mm_HandSolder
R102: R_4.7k; R_0805_2012Metric_Pad1.20x1.40mm_HandSolder
R103, R109, R110, R111, R112, R114, R115, R202, R302: R_10k; R_0805_2012Metric_Pad1.20x1.40mm_HandSolder
R104, R105, R106, R107, R108, R113: R_750; R_0805_2012Metric_Pad1.20x1.40mm_HandSolder
R201, R203, R301, R303: R_200; R_0805_2012Metric_Pad1.20x1.40mm_HandSolder
U1: Teensy3.6_All_Pins; Teensy35_36_All_Pins
U2: PA16165_Breakout
U3: MPL3115A2_Breakout
U4: BNO055_Breakout
U5: RFM69HCW_Breakout
U201, U301: TPS2113ADRBR; TSSOP-8_4.4x3mm_P0.65mm

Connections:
/3.3V: D105.2, J103.1, J104.1, R114.1, R115.1, U1.15, U1.51, U2.8, U3.1, U4.1, U5.1
/BAT1: BT101.1, C201.1, C301.1, R101.1, U201.8, U301.8
/BAT2: BT102.1, C202.1, C302.1, U201.6, U301.6
/BUZZER: BZ101.1, U1.6
/CS0: U1.12, U5.8
/E-MATCH_TRIGGER_1: R103.2, U1.35
/E-MATCH_TRIGGER_2: R109.2, U1.36
/EMATCH_1+: J101.1, J109.1, Q101.2, R111.2
/EMATCH_2+: J102.1, J110.1, Q102.2, R112.2
/KEY_SWITCH_DIGITAL: J103.2, J104.2, R110.1, U1.34
/LED_0: D106.2, U1.7
/LED_1: D101.2, U1.8
/LED_2: D102.2, U1.9
/LED_3: D103.2, U1.10
/LED_4: D104.2, U1.11
/MISO0: U1.14, U5.6
/MOSI0: U1.13, U5.7
/PWM: U1.4, U5.9
/RX1: U1.2, U2.6
/SCK: U1.40, U5.5
/SCL0: U1.46, U3.6, U4.5
/SCL2: U1.5, U5.4
/SDA0: U1.45, U3.7, U4.4
/TPS2113A for E-match/VSNS: R101.2, R102.1, U201.3, U301.3
/TPS_1_STAT: R114.2, R302.2, U1.32, U301.1
/TPS_2_STAT: R115.2, R202.2, U1.33, U201.1
/TX1: U1.3, U2.5
/V_EMATCH: J101.2, J102.2, J105.1, J107.1, J109.2, J110.2, R111.1, R112.1
/V_EMATCH_TO_KEY_SWITCH: C203.1, J105.2, J107.2, R202.1, U201.7
/V_TEENSY: C101.1, C303.1, R302.1, U1.53, U301.7
GND: BT101.2, BT102.2, BZ101.2, C101.2, C201.2, C202.2, C203.2, C301.2, C302.2, C303.2, Q101.3, Q102.3, R102.2, R104.2, R105.2, R106.2, R107.2, R108.2, R110.2, R113.2, R203.1, R303.1, U1.1, U1.39, U2.7, U3.2, U4.3, U5.2, U201.2, U201.5, U301.2, U301.5
unnamed: D101.1, R104.1
unnamed: D102.1, R105.1
unnamed: D103.1, R106.1
unnamed: D104.1, R107.1
unnamed: D105.1, R108.1
unnamed: D106.1, R113.1
unnamed: Q101.1, R103.1
unnamed: Q102.1, R109.1
unnamed: R201.1, R203.2
unnamed: R201.2, U201.4
unnamed: R301.1, R303.2
unnamed: R301.2, U301.4

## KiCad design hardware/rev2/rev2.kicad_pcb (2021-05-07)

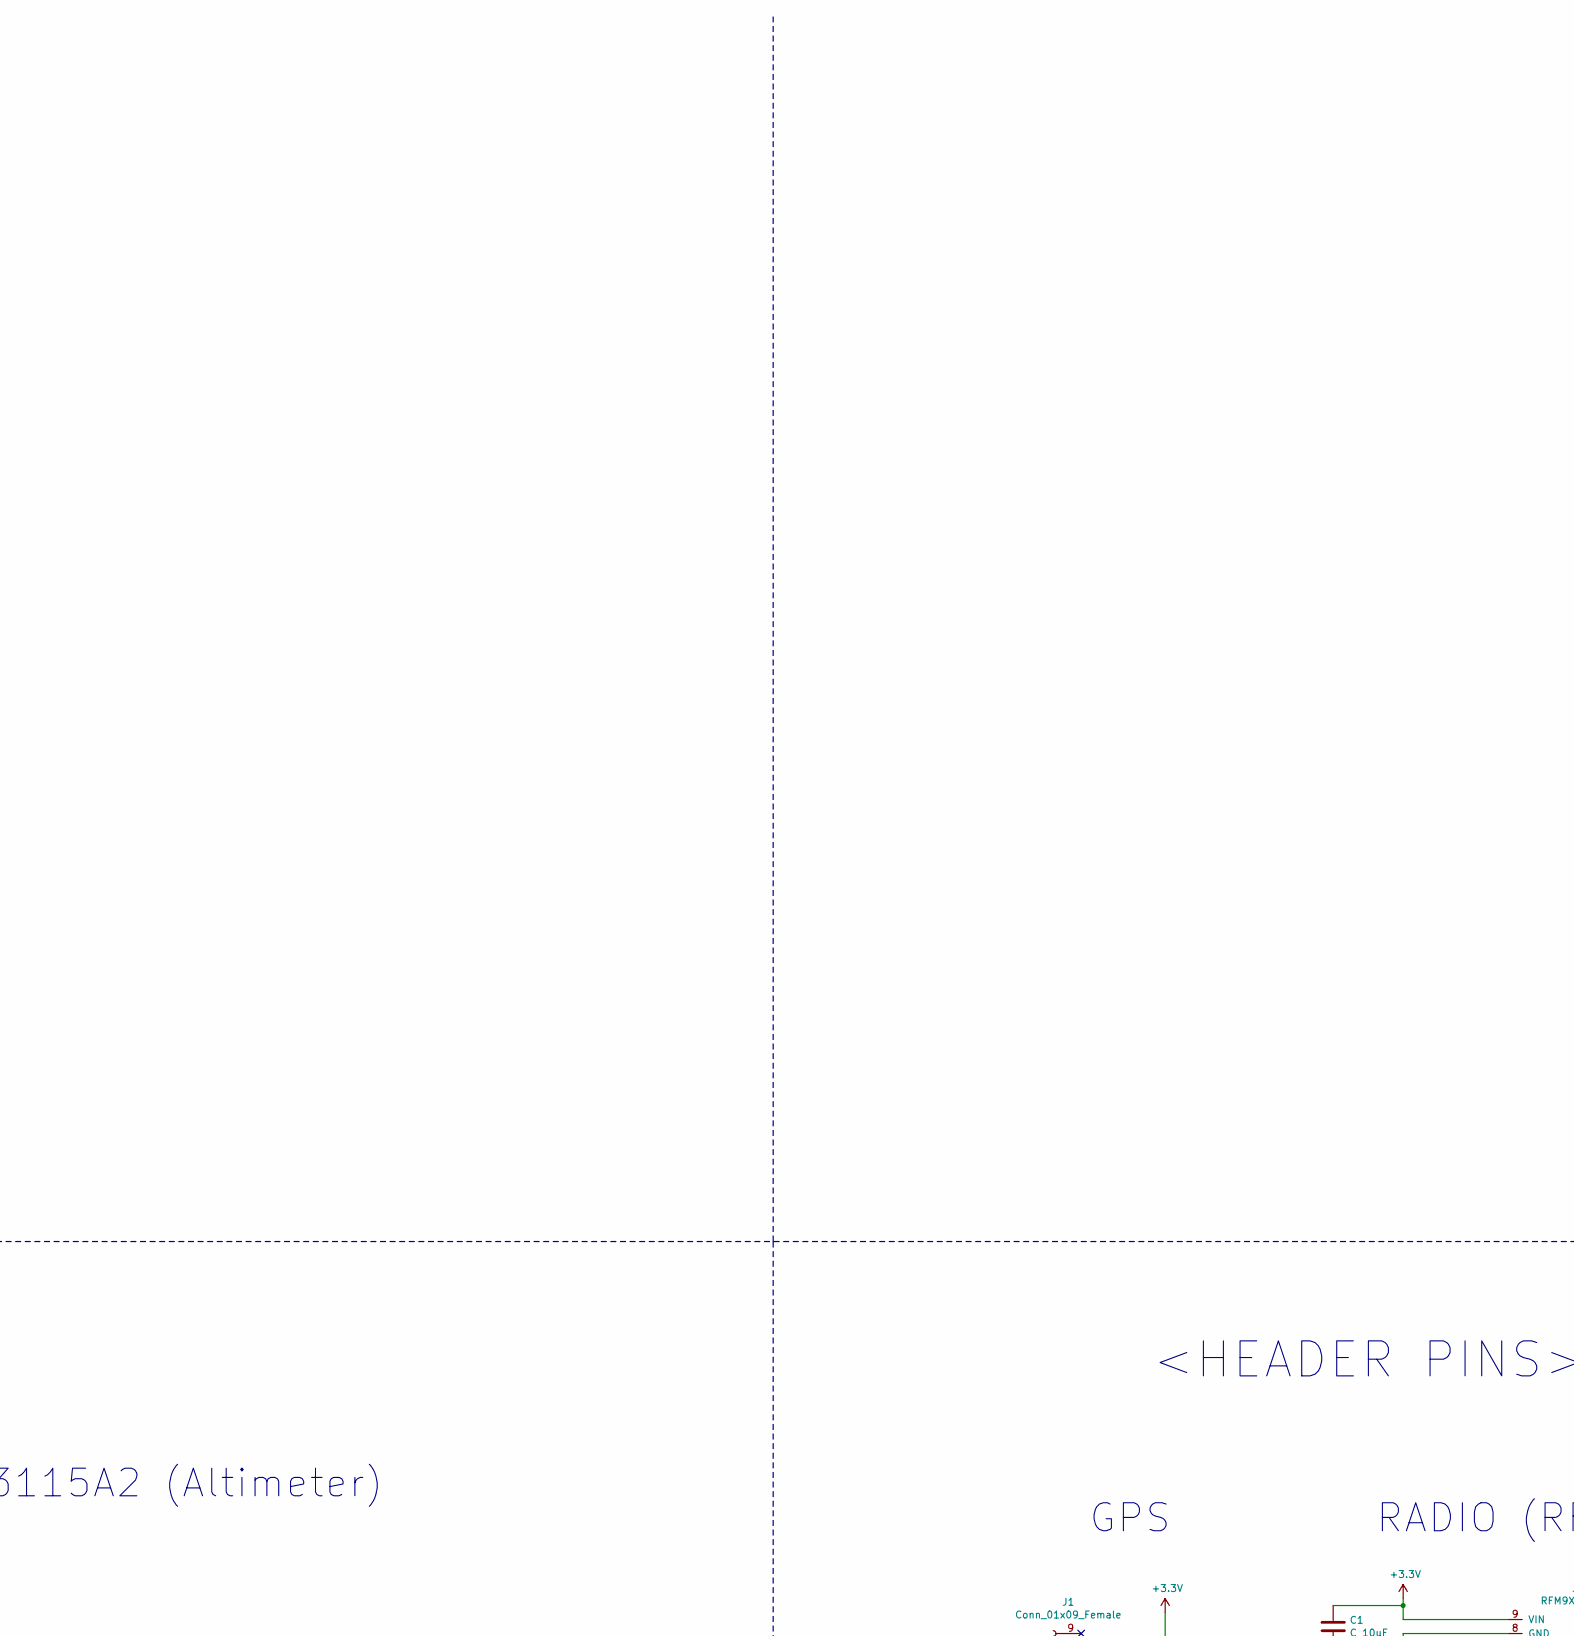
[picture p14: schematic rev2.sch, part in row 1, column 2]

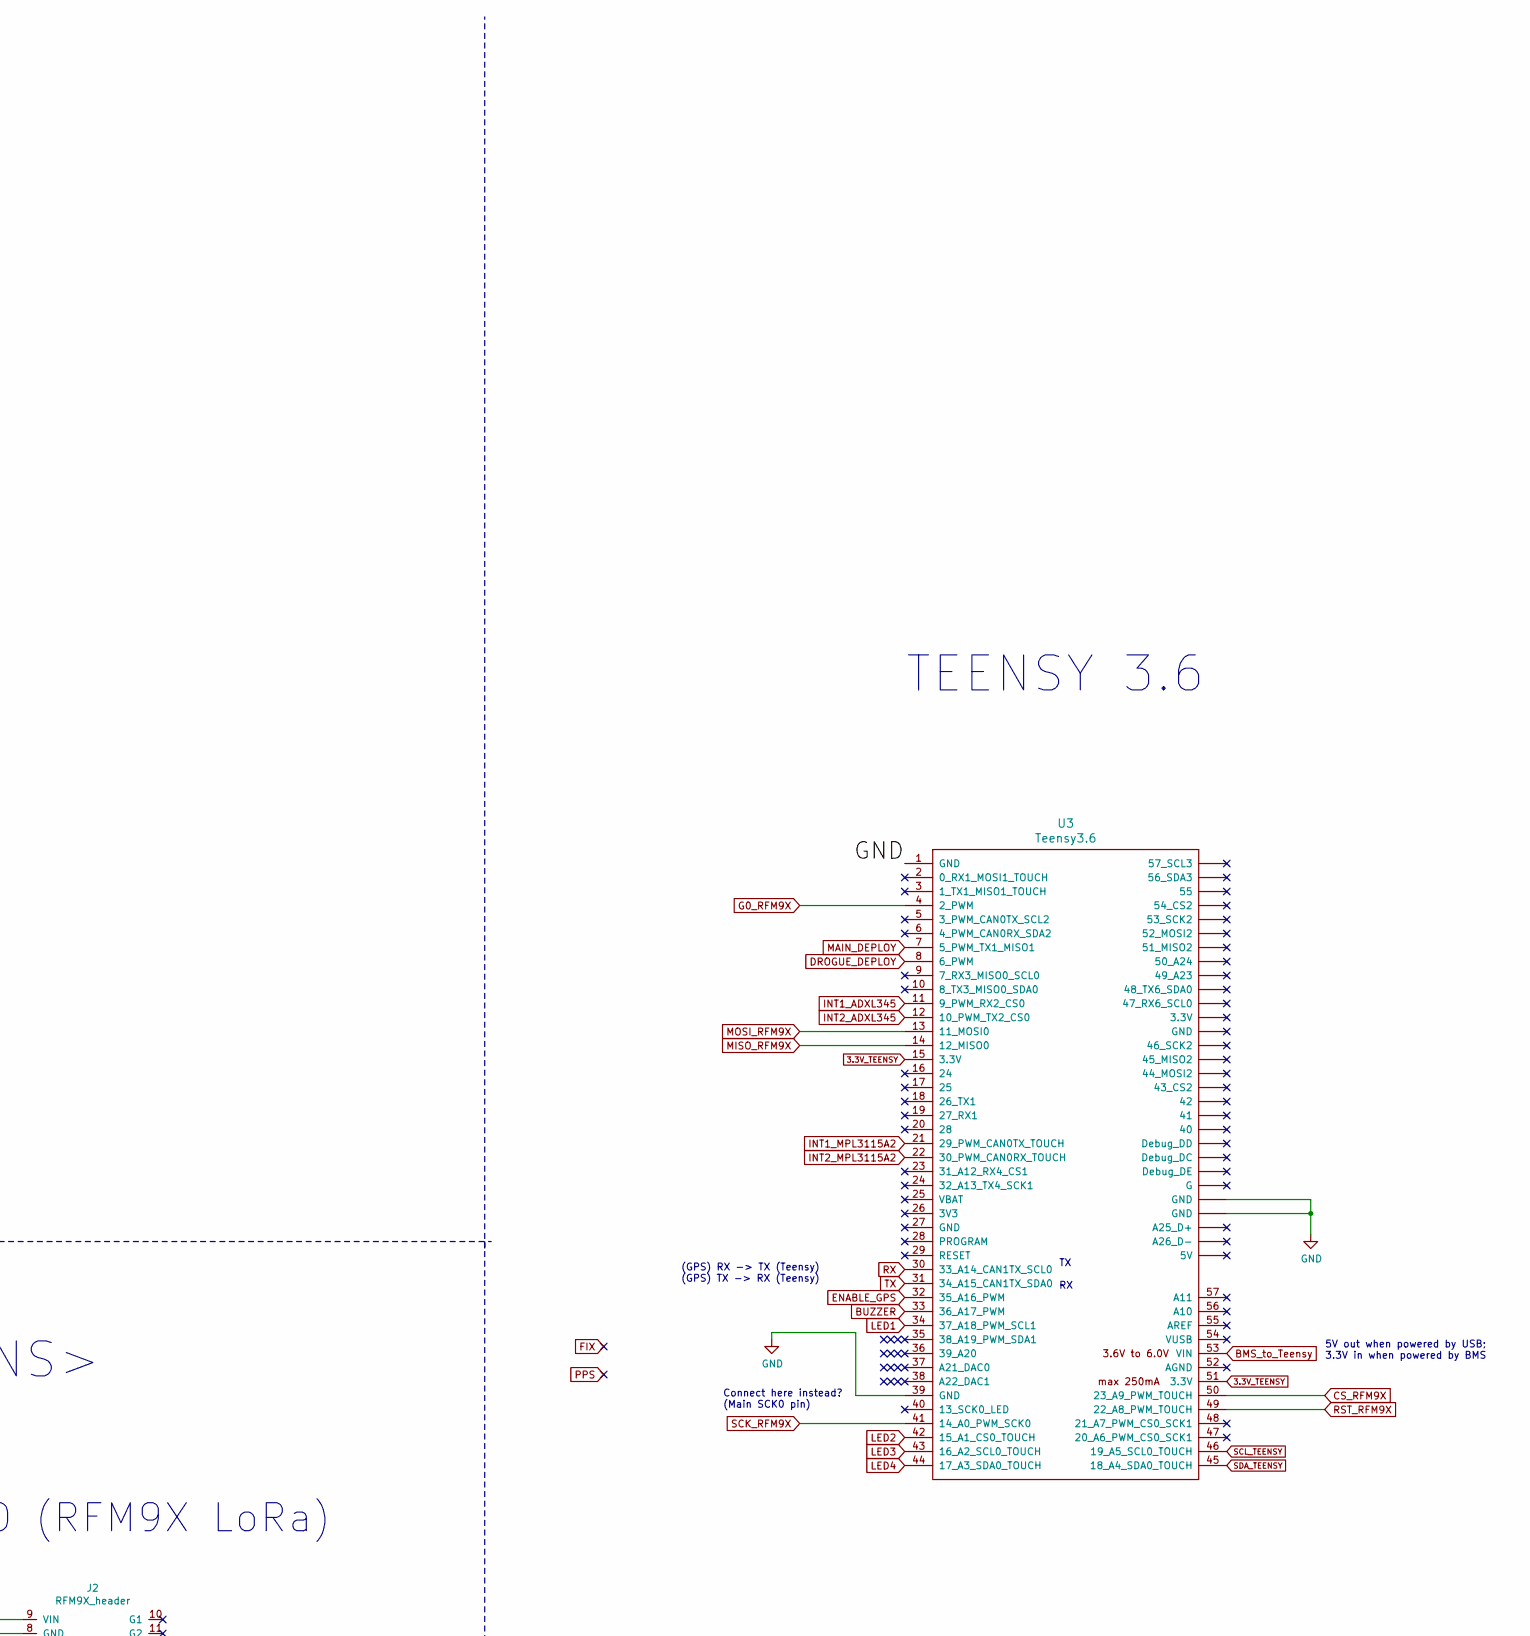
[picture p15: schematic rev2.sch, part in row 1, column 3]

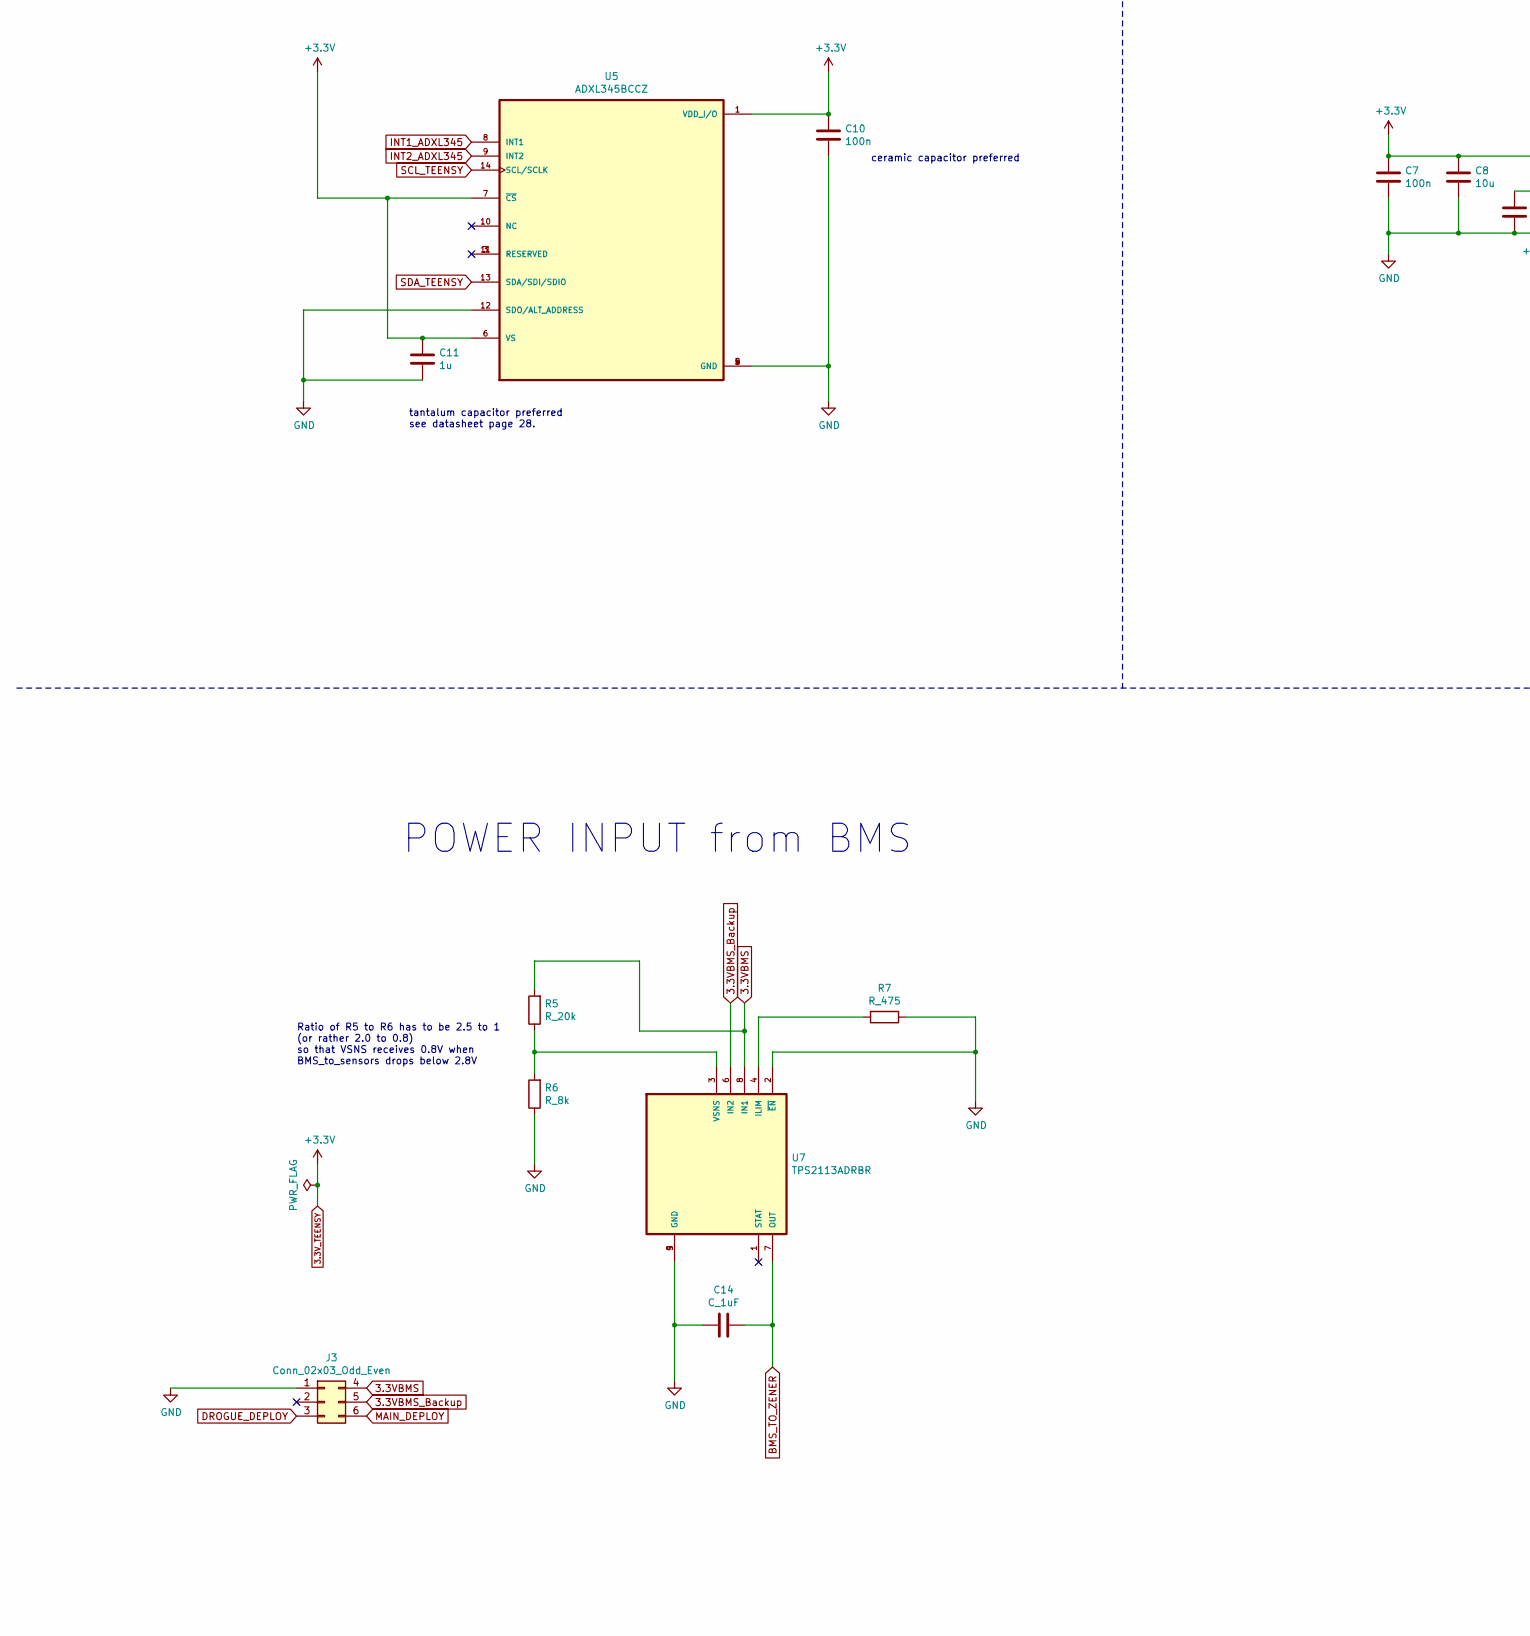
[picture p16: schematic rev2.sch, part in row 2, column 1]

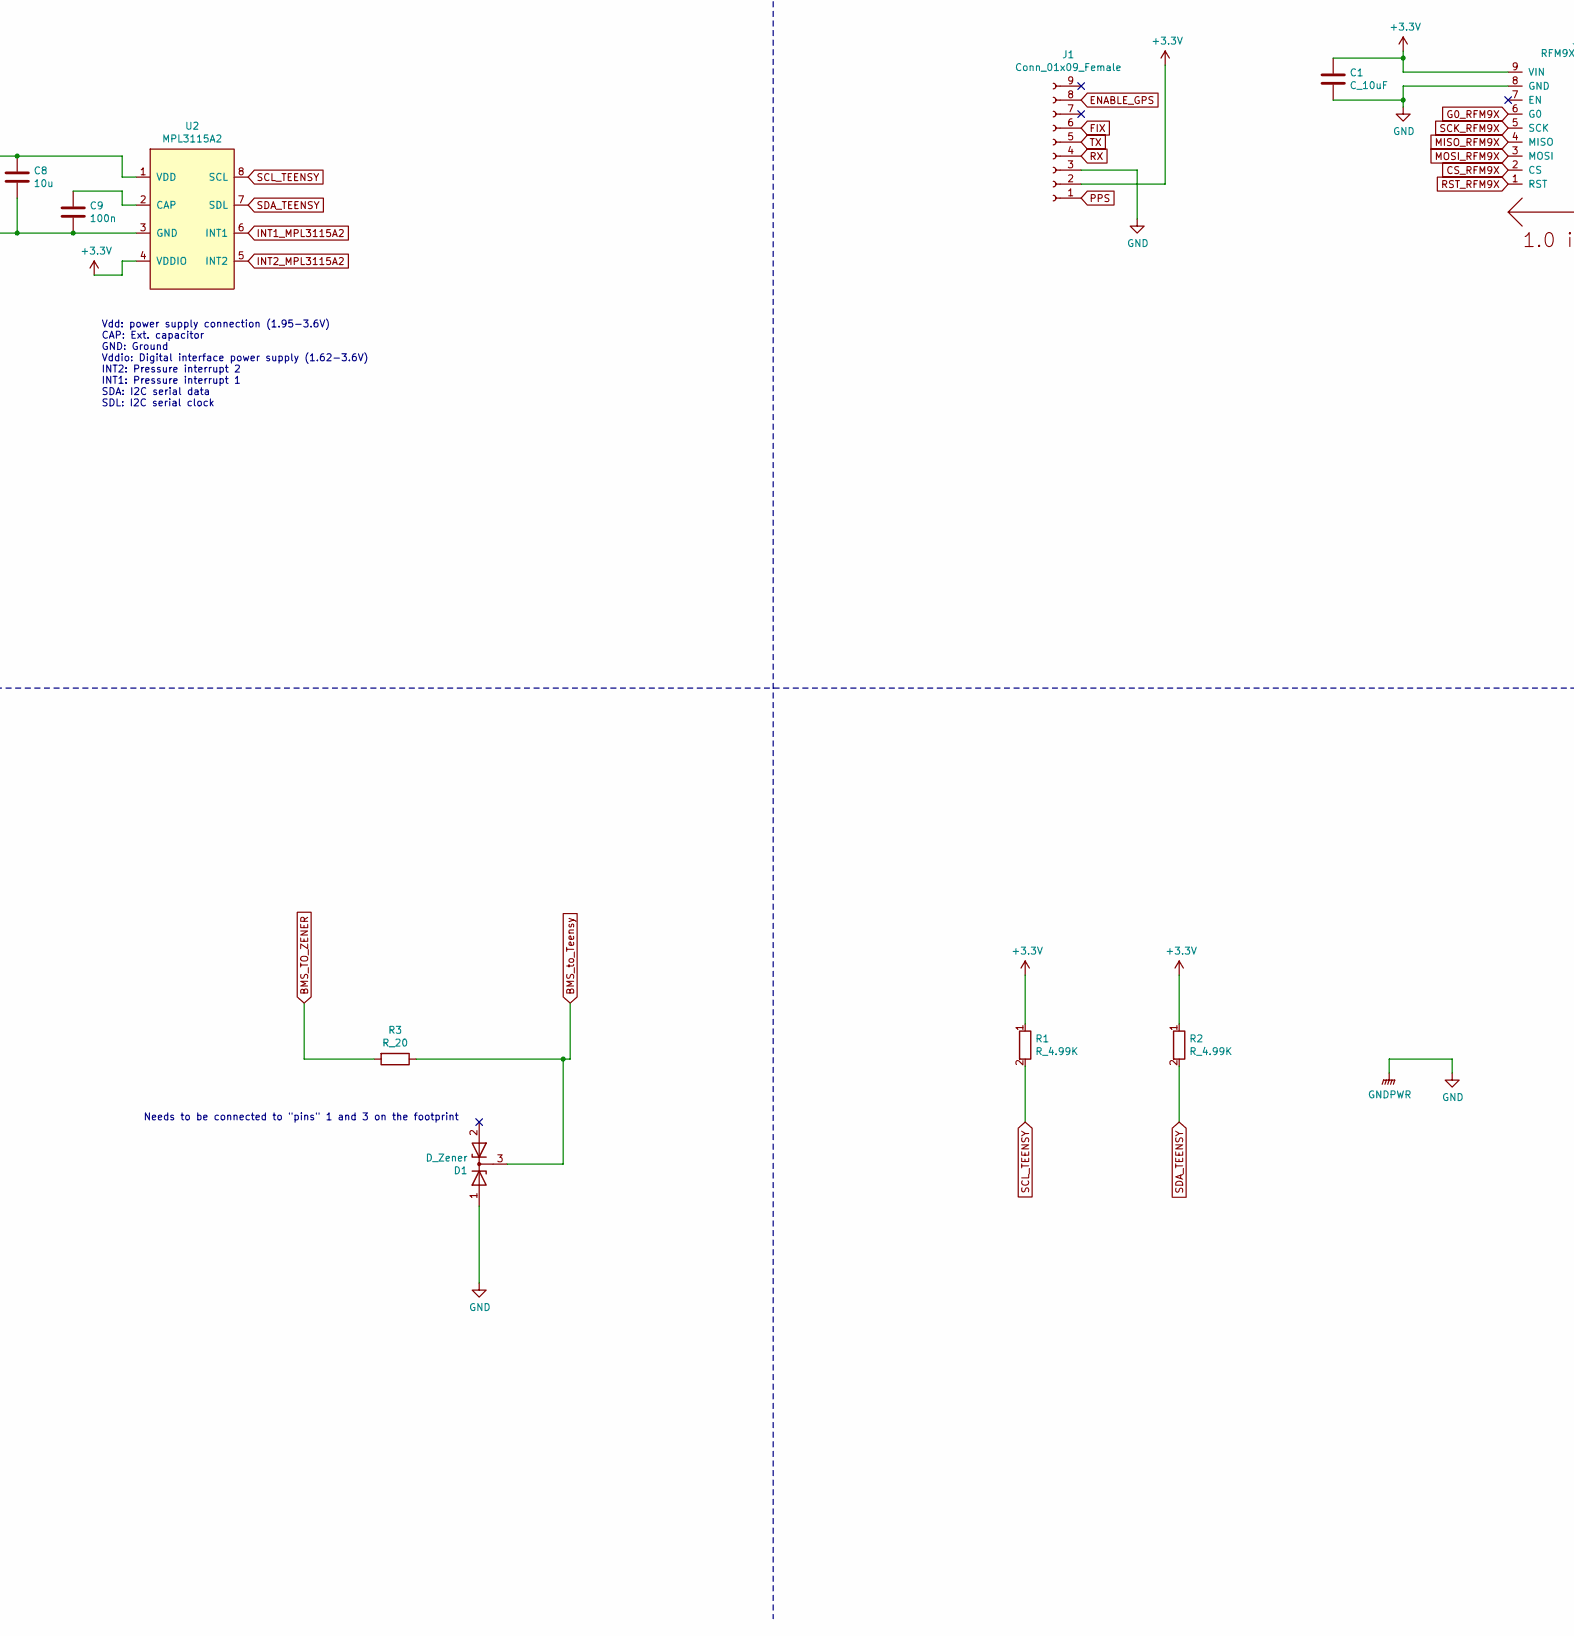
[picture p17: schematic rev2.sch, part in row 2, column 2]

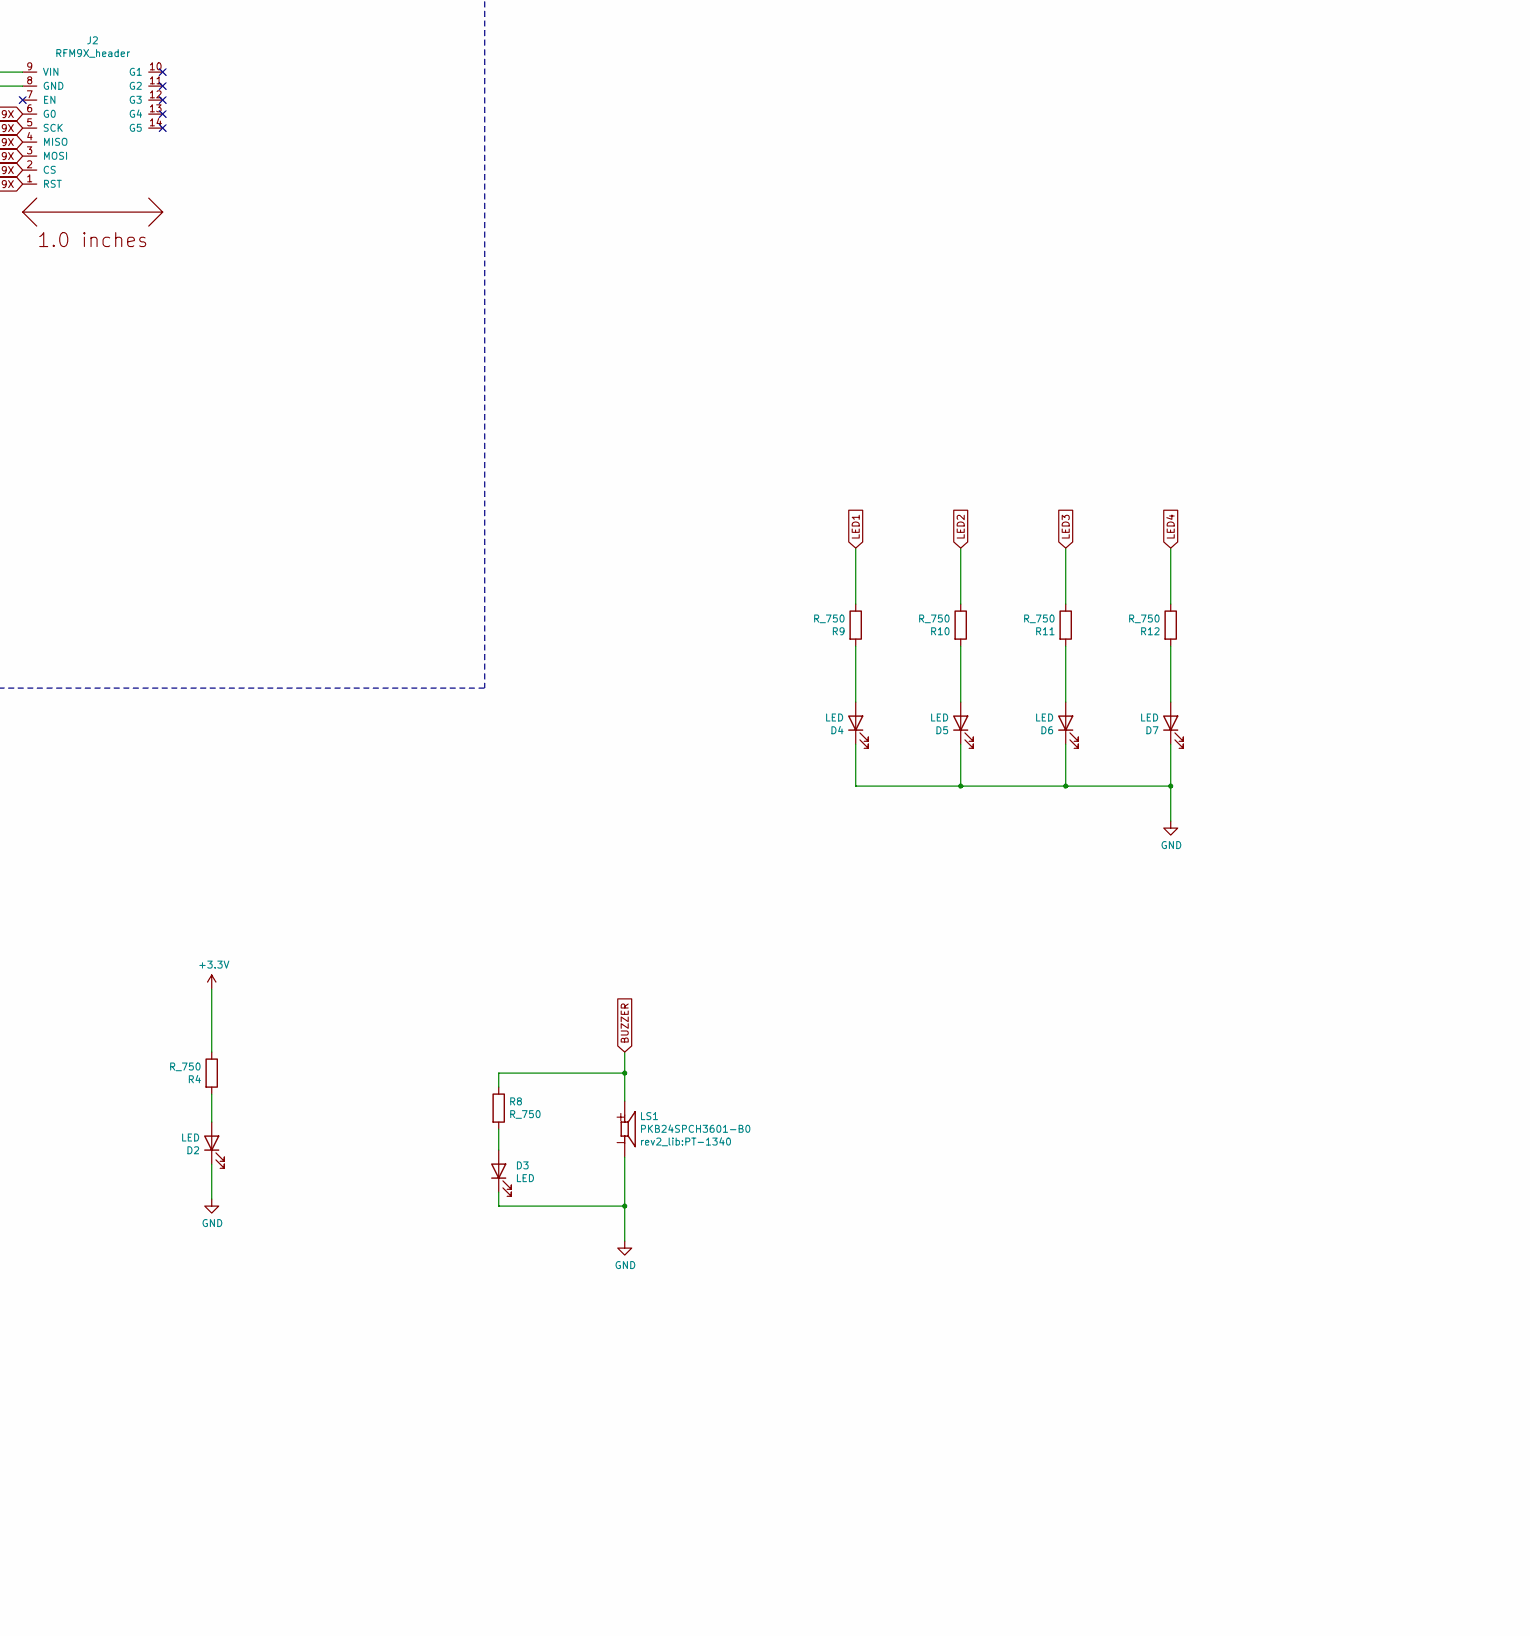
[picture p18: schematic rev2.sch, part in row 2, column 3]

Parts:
C1: C_10uF; C_0805_OEM; MPN 1276-1052-1-ND
C7, C9: 100n; C_0805_OEM
C8: 10u; C_0805_OEM
C10: 100n; C_0805_OEM; MPN 478-3352-1-ND
C11: 1u; C_0805_OEM; MPN 1276-2887-1-ND
C14: C_1uF; C_0805_OEM; MPN 1276-2887-1-ND
D1: D_Zener; SOT-23
D2, D3, D4, D5, D6, D7: LED; AA3528LSECKT-J4
J1: Conn_01x09_Female; PinSocket_1x09_P2.54mm_Vertical
J2: RFM9X_header
J3: Conn_02x03_Odd_Even; Molex_Nano-Fit_105312-1106
LS1: PKB24SPCH3601-B0; PT-1340; PARTREV March 24, 2017
R1, R2: R_4.99K; R_0805_OEM
R3: R_20; R_0805_OEM
R4, R8, R9, R10, R11, R12: R_750; R_0805_OEM
R5: R_20k; R_0805_OEM; MPN 311-475CRCT-ND
R6: R_8k; R_0805_OEM; MPN 311-475CRCT-ND
R7: R_475; R_0805_OEM; MPN 311-475CRCT-ND
U2: MPL3115A2
U3: Teensy3.6; Teensy3-6
U5: ADXL345BCCZ; ADXL345
U7: TPS2113ADRBR

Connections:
3.3VBMS: J3.4, R5.2, U7.8 (IN1)
3.3VBMS_Backup: J3.5, U7.6 (IN2)
3.3V_TEENSY: C1.1, C7.1, C8.1, C10.1, C11.1, J1.2, J2.9 (VIN), R1.1, R2.1, R4.1, U2.1 (VDD), U2.4 (VDDIO), U3.15 (3.3V), U3.51 (3.3V), U5.1 (VDD_I/O), U5.6 (VS), U5.7 (~CS)
BMS_TO_ZENER: C14.1, R3.2, U7.7 (OUT)
BMS_to_Teensy: D1.3 (K), R3.1, U3.53 (VIN)
BUZZER: LS1.P, R8.1, U3.33 (36_A17_PWM)
CS_RFM9X: J2.2 (CS), U3.50 (23_A9_PWM_TOUCH)
DROGUE_DEPLOY: J3.3, U3.8 (6_PWM)
ENABLE_GPS: J1.8, U3.32 (35_A16_PWM)
FIX: J1.6
G0_RFM9X: J2.6 (G0), U3.4 (2_PWM)
GND: C1.2, C7.2, C8.2, C9.2, C10.2, C11.2, C14.2, D1.1 (A), D2.1 (K), D3.1 (K), D4.1 (K), D5.1 (K), D6.1 (K), D7.1 (K), J1.3, J2.8 (GND), J3.1, LS1.N, R6.1, R7.1, U2.3 (GND), U3.1 (GND), U3.39 (GND), U3.~ (3.3V), U5.2 (GND), U5.4 (GND), U5.5 (GND), U5.12 (SDO/ALT_ADDRESS), U7.2 (~EN), U7.5 (GND), U7.9 (GND)
INT1_ADXL345: U3.11 (9_PWM_RX2_CS0), U5.8 (INT1)
INT1_MPL3115A2: U2.6 (INT1), U3.21 (29_PWM_CAN0TX_TOUCH)
INT2_ADXL345: U3.12 (10_PWM_TX2_CS0), U5.9 (INT2)
INT2_MPL3115A2: U2.5 (INT2), U3.22 (30_PWM_CAN0RX_TOUCH)
LED1: R9.1, U3.34 (37_A18_PWM_SCL1)
LED2: R10.1, U3.42 (15_A1_CS0_TOUCH)
LED3: R11.1, U3.43 (16_A2_SCL0_TOUCH)
LED4: R12.1, U3.44 (17_A3_SDA0_TOUCH)
MAIN_DEPLOY: J3.6, U3.7 (5_PWM_TX1_MISO1)
MISO_RFM9X: J2.4 (MISO), U3.14 (12_MISO0)
MOSI_RFM9X: J2.3 (MOSI), U3.13 (11_MOSI0)
unnamed: C9.1, U2.2 (CAP)
unnamed: D2.2 (A), R4.2
unnamed: D3.2 (A), R8.2
unnamed: D4.2 (A), R9.2
unnamed: D5.2 (A), R10.2
unnamed: D6.2 (A), R11.2
unnamed: D7.2 (A), R12.2
unnamed: R5.1, R6.2, U7.3 (VSNS)
unnamed: R7.2, U7.4 (ILIM)
unnamed: U5.3 (RESERVED), U5.11 (RESERVED)
PPS: J1.1
RST_RFM9X: J2.1 (RST), U3.49 (22_A8_PWM_TOUCH)
RX: J1.4, U3.30 (33_A14_CAN1TX_SCL0)
SCK_RFM9X: J2.5 (SCK), U3.41 (14_A0_PWM_SCK0)
SCL_TEENSY: R1.2, U2.8 (SCL), U3.46 (19_A5_SCL0_TOUCH), U5.14 (SCL/SCLK)
SDA_TEENSY: R2.2, U2.7 (SDL), U3.45 (18_A4_SDA0_TOUCH), U5.13 (SDA/SDI/SDIO)
TX: J1.5, U3.31 (34_A15_CAN1TX_SDA0)

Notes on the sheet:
MPL3115A2 (Altimeter)
Vdd: power supply connection (1.95-3.6V) CAP: Ext. capacitor GND: Ground Vddio: Digital interface power supply (1.62-3.6V) INT2: Pressure interrupt 2 INT1: Pressure interrupt 1 SDA: I2C serial data SDL: I2C serial clock
Pull-up resistors exist on another part of the schematic.
ADXL345
RADIO (RFM9X LoRa)
POWER INPUT from BMS
GPS
ceramic capacitor preferred
tantalum capacitor preferred see datasheet page 28.
TX RX
(GPS) RX -> TX (Teensy) (GPS) TX -> RX (Teensy)
5V out when powered by USB; 3.3V in when powered by BMS
<HEADER PINS>
TEENSY 3.6
Ratio of R5 to R6 has to be 2.5 to 1 (or rather 2.0 to 0.8) so that VSNS receives 0.8V when BMS_to_sensors drops below 2.8V
Needs to be connected to "pins" 1 and 3 on the footprint
Connect here instead? (Main SCK0 pin)

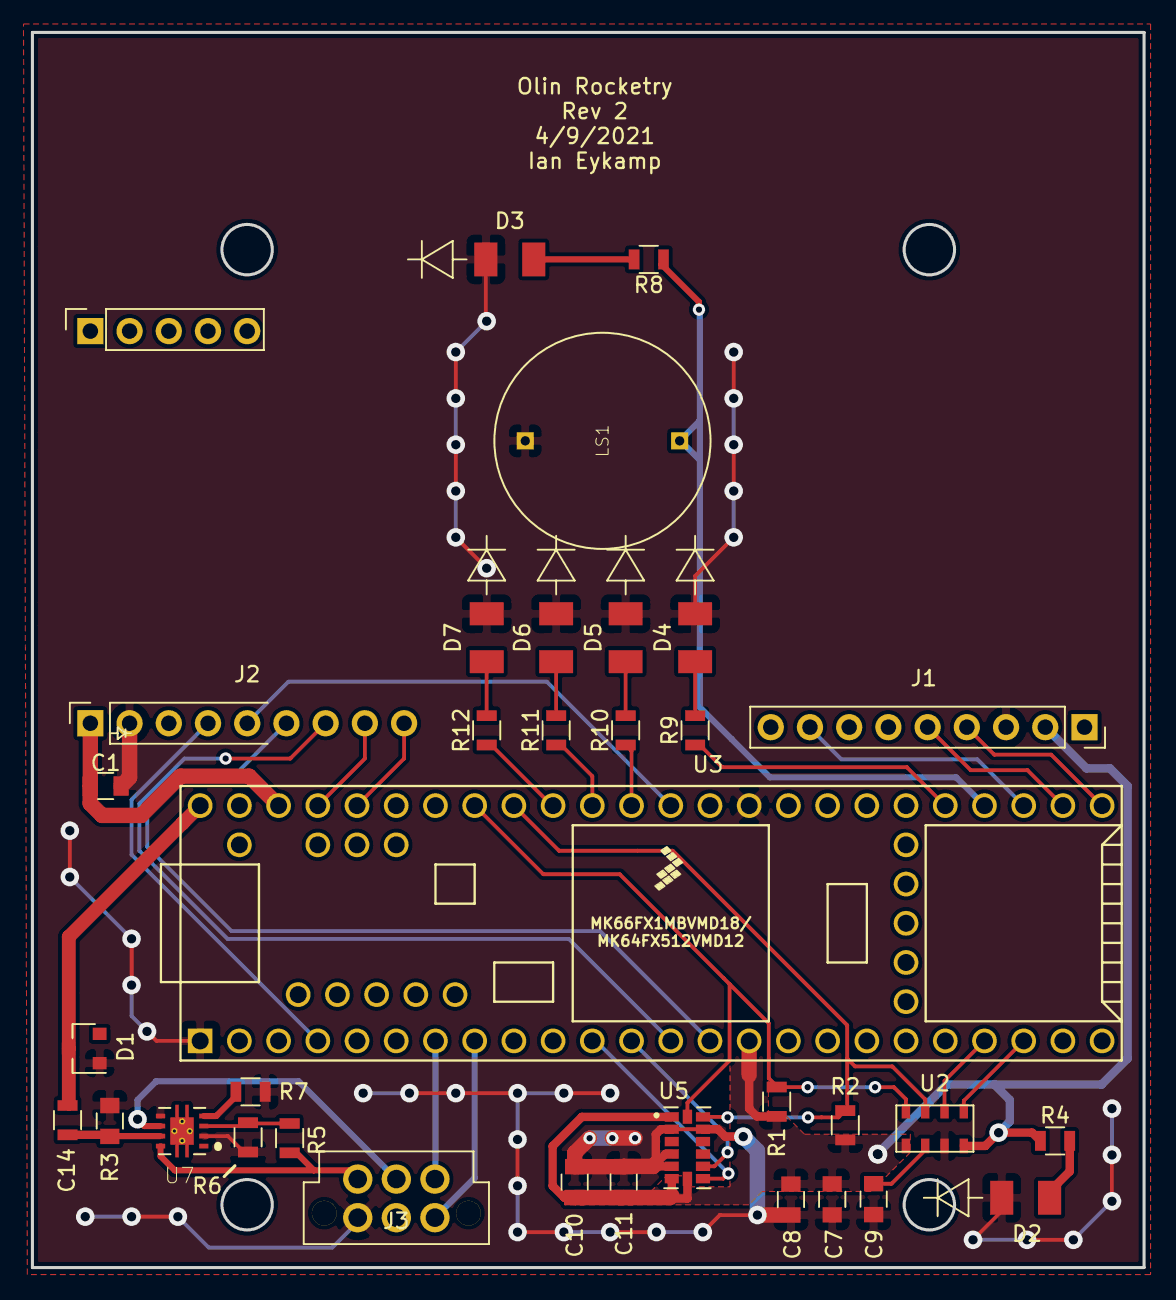
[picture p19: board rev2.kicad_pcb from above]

Board: 2 copper layers, 72.0 x 80.0 mm, 34 parts (1 on the bottom side), 38 nets.

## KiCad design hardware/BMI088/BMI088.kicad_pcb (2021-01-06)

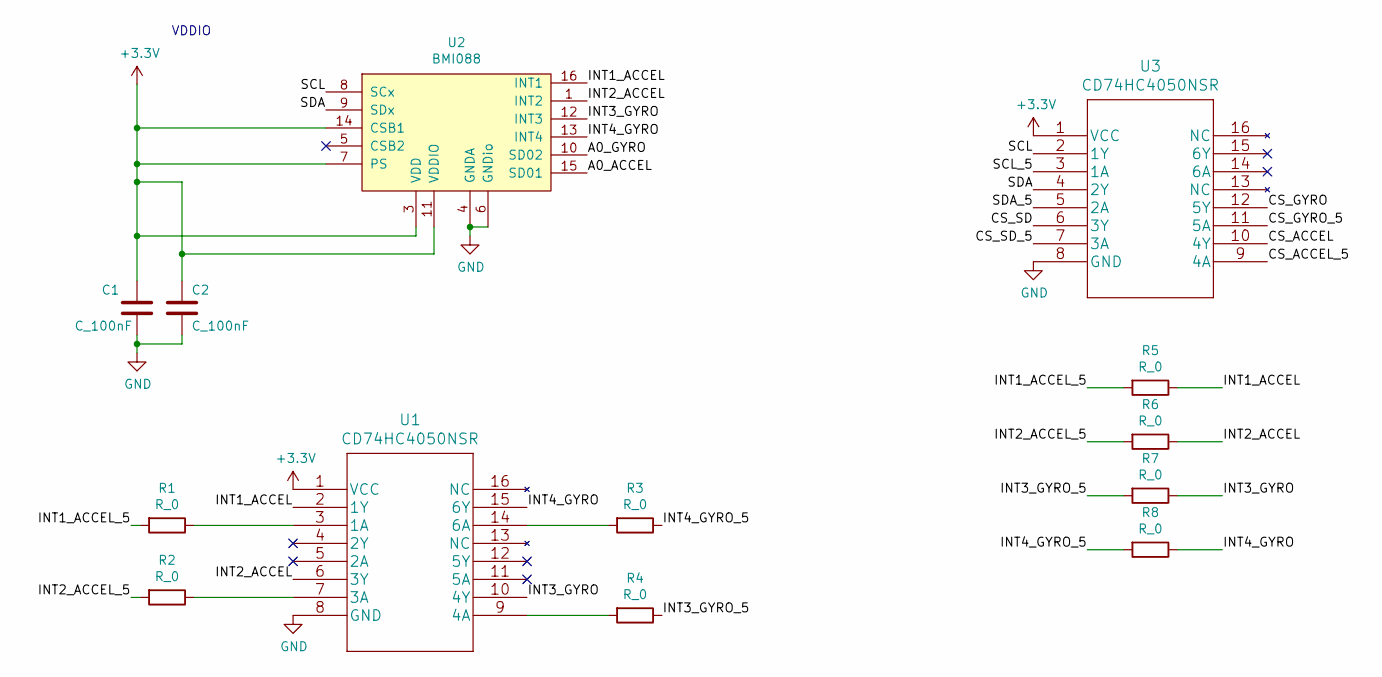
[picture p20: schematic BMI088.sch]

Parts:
C1, C2: C_100nF; C_0603_1608Metric; MPN 1276-6717-1-ND
R1, R2, R3, R4, R5, R6, R7, R8: R_0; R_0603_1608Metric; MPN P0.0GCT-ND
U1, U3: CD74HC4050NSR
U2: BMI088; bmi088

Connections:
+3V3: C1.1, C2.1, U1.1 (VCC), U2.3 (VDD), U2.7 (PS), U2.11 (VDDIO), U2.14 (CSB1), U3.1 (VCC)
/A0_ACCEL: U2.15 (SD01)
/A0_GYRO: U2.10 (SD02)
/CS_ACCEL: U3.10 (4Y)
/CS_ACCEL_5: U3.9 (4A)
/CS_GYRO: U3.12 (5Y)
/CS_GYRO_5: U3.11 (5A)
/CS_SD: U3.6 (3Y)
/CS_SD_5: U3.7 (3A)
/INT1_ACCEL: R5.1, U1.2 (1Y), U2.16 (INT1)
/INT1_ACCEL_5: R1.2, R5.2
/INT2_ACCEL: R6.1, U1.6 (3Y), U2.1 (INT2)
/INT2_ACCEL_5: R2.2, R6.2
/INT3_GYRO: R7.1, U1.10 (4Y), U2.12 (INT3)
/INT3_GYRO_5: R4.1, R7.2
/INT4_GYRO: R8.1, U1.15 (6Y), U2.13 (INT4)
/INT4_GYRO_5: R3.1, R8.2
/SCL: U2.8 (SCx), U3.2 (1Y)
/SCL_5: U3.3 (1A)
/SDA: U2.9 (SDx), U3.4 (2Y)
/SDA_5: U3.5 (2A)
GND: C1.2, C2.2, U1.8 (GND), U2.4 (GNDA), U2.6 (GNDio), U3.8 (GND)
unnamed: R1.1, U1.3 (1A)
unnamed: R2.1, U1.7 (3A)
unnamed: R3.2, U1.14 (6A)
unnamed: R4.2, U1.9 (4A)

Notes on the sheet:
VDDIO

Board: 2 copper layers, 13 parts (0 on the bottom side), 16 nets, no tracks yet.

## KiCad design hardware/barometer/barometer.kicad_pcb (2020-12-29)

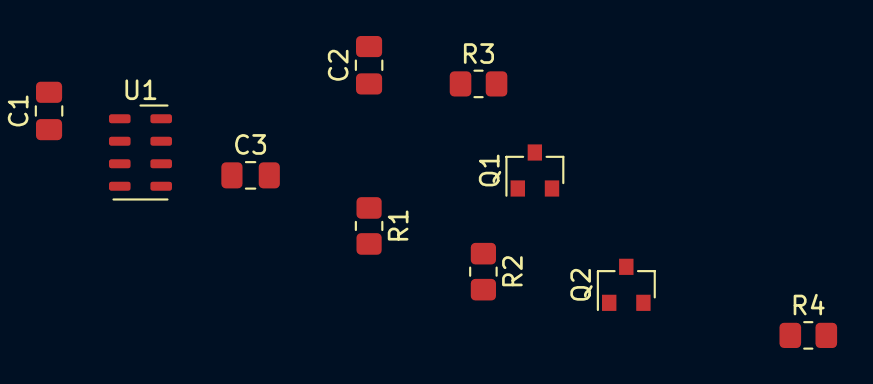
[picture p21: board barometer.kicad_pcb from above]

Board: 2 copper layers, 10 parts (0 on the bottom side), 7 nets, no tracks yet.

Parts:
C1, C3: 100nF; C_0805_2012Metric_Pad1.18x1.45mm_HandSolder
C2: 10uF; C_0805_2012Metric_Pad1.18x1.45mm_HandSolder
Q1, Q2: BSS138; SOT-23
R1, R2, R3, R4: R_10K; R_0805_2012Metric_Pad1.20x1.40mm_HandSolder
U1: MPL3115A2; NXP_LGA-8_3x5mm_P1.25mm_H1.1mm

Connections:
+3V3: Q1.1, Q2.1, R1.1, R2.1
/SCL_3V: Q2.2, R2.2
/SCL_RAW: Q2.3, R4.2
/SDA_3V: Q1.2, R1.2
/SDA_RAW: Q1.3, R3.2
GND: C1.2, C2.1, C2.2, C3.1, C3.2, R3.1, R4.1, U1.1, U1.3
unnamed: C1.1, U1.2

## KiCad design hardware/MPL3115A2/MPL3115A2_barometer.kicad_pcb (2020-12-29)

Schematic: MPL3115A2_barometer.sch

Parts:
C1, C3: 100n; C_0805_OEM
C2: 10u; C_0805_OEM
TP1: TestPoint; TestPoint_Keystone_5010-5014_Multipurpose
U1: MPL3115A2

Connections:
GND: C1.2, C2.2, C3.2, U1.3
INT1: U1.6
INT2: U1.5
unnamed: C3.1, TP1.1, U1.2
SCL: U1.8
SDL: U1.7
VDDIO: C1.1, C2.1, U1.1, U1.4

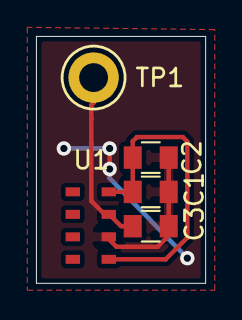
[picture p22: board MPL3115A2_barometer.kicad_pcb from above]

Board: 2 copper layers, 9.4 x 13.7 mm, 5 parts (0 on the bottom side), 3 nets.

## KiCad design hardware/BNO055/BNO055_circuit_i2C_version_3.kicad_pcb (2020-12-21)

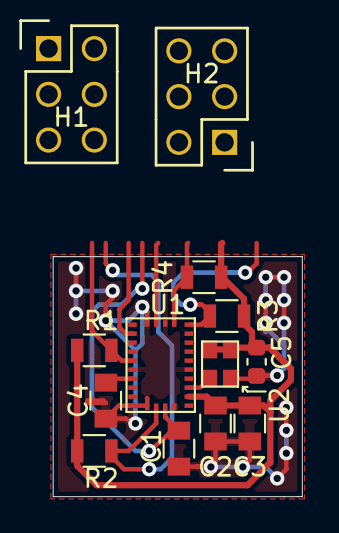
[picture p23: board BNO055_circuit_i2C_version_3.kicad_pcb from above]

Board: 2 copper layers, 13.8 x 13.3 mm, 13 parts (0 on the bottom side), 11 nets.

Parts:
C1, C4: 100nF; C_0805_OEM
C2: 6.8nF; C_0805_OEM
C3: 120nF; C_0805_OEM
C5: 0.01u; C_0603_1608Metric
H1, H2: Header_2x3; Pin_Header_Straight_2x03
R1: Optional 10k; R_0805_OEM
R2: Pull-up 10k; R_0805_OEM
R3, R4: Rpull; R_0805_OEM
U1: BNO055
U2: ASDMB-xxxMHz; ASDK2-32.768KHZ-LR-T3

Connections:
COM3: H2.1, U1.17
GND: C1.2, C2.1, C3.1, C4.2, C5.1, H1.1, U1.2, U1.5, U1.6, U1.10, U1.16, U1.18, U1.25, U2.2
INT: H2.6, U1.14
unnamed: C4.1, U1.9
OptionalOSCinput: U1.27, U2.3
SCL: H2.3, R4.2, U1.19
SDA: H2.5, R3.2, U1.20
VDD: C1.1, H1.3, U1.3
VDDIO: C2.2, C3.2, C5.2, H1.5, R1.1, R2.1, R3.1, R4.1, U1.28, U2.1, U2.4
nBOOT_LOAD_PIN: H2.2, R2.2, U1.4
nRESET: H2.4, R1.2, U1.11

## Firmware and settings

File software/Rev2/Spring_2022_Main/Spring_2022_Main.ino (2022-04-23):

//General
#include <Wire.h>
#include <SD.h>
#include <SPI.h>
#include <Adafruit_Sensor.h>//General sensor library
#include <Adafruit_BNO055.h>//IMU
//#include <Adafruit_MPL3115A2.h>//Altitude
#include <utility/imumaths.h>//MathM
#include "phoenix_IV_functions.h"
#include "dataPoint.h"//Datapoint
#include <RH_RF95.h>//Radio
#define RFM95_CS 10//Radio
#define RFM95_RST 2//Radio
#define RFM95_INT 3//Radio
#define RF95_FREQ 915.0//Radio Change to 434.0 or other frequency, must match RX's freq!
#define buzzer 4//buzzer to teensy pin 4
#define ALTMODE 1; //comment out for barometer mode; default is altitude mode
//start altitude to calculate mean sea level pressure in meters
#define ALTBASIS 32 //CHANGE BEFORE LUANCH
//this altitude must be known (or provided by GPS etc.)

const int SENSORADDRESS = 0x60; // address specific to the MPL3115A1, value found in datasheet
 
float altsmooth = 0; //for exponential smoothing
byte IICdata[5] = {0,0,0,0,0}; //buffer for sensor data
//Create Instances of sensors
RH_RF95 rf95(RFM95_CS, RFM95_INT);//Radio Singleton instance of the radio driver
Adafruit_BNO055 bno = Adafruit_BNO055(55, 0x28);//IMU
//Adafruit_MPL3115A2 mpl;//Altimeter

//Creates list datapoint objects for flight during phase 3
const int batchSize = 500; 
dataPoint dataPoints[batchSize];
int currentDataPoint = 0;

//Global Variables
File myFile; //SD
float IMU[7]={0.0,0.0,0.0,0.0,0.0,0.0,0.0};
float altitude = 0.0;
float GPSArray[2] = {0.0, 0.0};

const float Pi = 3.14159;
// Puts the rocket in the calibration phase (phase 1)
// There are 6 phases: Calibration, pre keyswitch, Pre-Launch, Launch, Detection of Apogee, Detection of 1,000 feet on descent
short int phase = 0;
// Configure timers for aquiring sensor data
unsigned int long lastCallTime = millis();
unsigned int newcalltime;
// Minimum acceleration and altitude required to start launch phase
float minimumAltitude;
float minimumMainAltitude;

double state[3];//{altitude, velocity, acceleration}, set to initial altitude, 0, initial global z accel on first run 

//TODO: if change this value, also change Q in kalman_update
double p_cov[3][3] = {{3, 0, 0}, {0, 2, 0}, {0, 0, 1}};
bool firstKalman = true;
char buffer[50];
bool gatherData = false;

void setup(void)
{  
  Wire.begin();
  Serial.begin(9600);
  setupSensors();
}
void loop() {
    
  // Chooses loop to run through depending on what the phase is set to
  switch (phase) {

    // Calibration phase
    case 0:
      Serial.println("Phase 0:");
      while (phase == 0) {
          calibrationPhase();
          phase=1;
      }
      break;

    // Pre-Launch phase
    case 1:
      Serial.println("Phase 1:");
      while (phase == 1) {
          PreLaunch();
      }
      break;
    // After Keyswitch before luanch
    case 2:
      Serial.println("Phase 2:");
     newcalltime=millis();
      while (phase == 2) {
       AfterLaunch();
      }
      break;
      
    // Lauched but before apogee
    case 3:
      Serial.println("Phase 3:");
      while (phase == 3) {
          BeforeApogee();
      }
      break;
      
    // After apogee before main deploy
    case 4:
      Serial.println("Phase 4:");
      while (phase == 4) {
       BeforeMain();
      }
      break;
      
  //After main deploy
   case 5:
      Serial.println("Phase 5:");
        while (phase == 5) {
          AfterMain();
        }
      }
}

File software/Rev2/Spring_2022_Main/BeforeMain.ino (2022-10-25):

 void BeforeMain(){
          fetchSensorData();
          lastCallTime = millis();
          addDataPoint();
           char *buffer1;
          buffer1= (char*) malloc(70*sizeof(char));
      sprintf(buffer1, "Time: %lu Phase: %d alt: %f",lastCallTime, phase, altitude);
       fetchRadio(buffer1);
       free(buffer1);
          if (altitude < minimumMainAltitude) {


            

            
            digitalWrite(A20, HIGH);
            delay(1000);
            digitalWrite(A20, LOW);

            
            phase = 5;
            SD_write();
          }
          }

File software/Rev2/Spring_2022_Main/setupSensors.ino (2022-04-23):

 void setupSensors(){
if(IIC_Read(0x0C) != 196){ //checks whether sensor is readable (who_am_i bit)
  Serial.println("i2c bad");
}
  IIC_Write(0x2D,0); //write altitude offset=0 (because calculation below is based on offset=0)
  //calculate sea level pressure by averaging a few readings
  Serial.println("Pressure calibration...");
  float buff[4];
  for (byte i=0;i<4;i++){
    IIC_Write(0x26, 0b00111011); //bit 2 is one shot mode, bits 4-6 are 128x oversampling
    IIC_Write(0x26, 0b00111001); //must clear oversampling (OST) bit, otherwise update will be once per second
    delay(550); //wait for sensor to read pressure (512ms in datasheet)
    IIC_ReadData(); //read sensor data
    buff[i] = Baro_Read(); //read pressure
    Serial.println(buff[i]);
  }
  float currpress=(buff[0]+buff[1]+buff[2]+buff[3])/4; //average over two seconds
 
  Serial.print("Current pressure: "); Serial.print(currpress); Serial.println(" Pa");
  //calculate pressure at mean sea level based on a given altitude
  float seapress = currpress/pow(1-ALTBASIS*0.0000225577,5.255877);
  Serial.print("Sea level pressure: "); Serial.print(seapress); Serial.println(" Pa");
  Serial.print("Temperature: ");
  Serial.print(IICdata[3]+(float)(IICdata[4]>>4)/16); Serial.println(" C");
 
  // This configuration option calibrates the sensor according to
  // the sea level pressure for the measurement location (2 Pa per LSB)
  IIC_Write(0x14, (unsigned int)(seapress / 2)>>8);//IIC_Write(0x14, 0xC3); // BAR_IN_MSB (register 0x14):
  IIC_Write(0x15, (unsigned int)(seapress / 2)&0xFF);//IIC_Write(0x15, 0xF3); // BAR_IN_LSB (register 0x15):
  // Configure Sensors
  
 
  // IMU
  if (!bno.begin())
  {
    Serial.print("No BNO055 detected");
    while (1);
  }
   bno.setExtCrystalUse(true);
  //Altimeter
//  if (!mpl.begin()) {
//    Serial.println("NO MPL3115A2 detected");
//    while(1);
//  }
//  mpl.setSeaPressure(1013.26);
  
  // Configure LED pins
  pinMode(6, OUTPUT);
  pinMode(7, OUTPUT);
  pinMode(8, OUTPUT);
  

 
//Radio
    pinMode(RFM95_RST, OUTPUT);
  digitalWrite(RFM95_RST, HIGH);

  Serial.println("Arduino LoRa TX Test!");

  // manual reset
  digitalWrite(RFM95_RST, LOW);
  delay(10);
  digitalWrite(RFM95_RST, HIGH);
  delay(10);

  while (!rf95.init()) {
    Serial.println("LoRa radio init failed");
    while (1);
  }
  Serial.println("LoRa radio init OK!");

  // Defaults after init are 434.0MHz, modulation GFSK_Rb250Fd250, +13dbM
  if (!rf95.setFrequency(RF95_FREQ)) {
    Serial.println("setFrequency failed");
    while (1);
  }
  Serial.print("Set Freq to: "); Serial.println(RF95_FREQ);
  rf95.setTxPower(23, false);

//Buzzer
pinMode(buzzer, OUTPUT);


 //Setup SD CARD
 // const int chipSelect = 4;
  // see if the card is present and can be initialized:
  char ch[70];
  if (!SD.begin(BUILTIN_SDCARD)) {
    Serial.println("Card failed, or not present");
    while (1);
  }
  else{
    Serial.println("Card initialized.");
    File dataFile = SD.open("flightData.txt", FILE_WRITE); // Not sure about this data type
    if (dataFile) {
           dataFile.println("Start");
     }
     dataFile.close(); // close the file
     File data1 = SD.open("flightData.txt"); // Not sure about this data type
     if (data1) {
          
          int count=0;
          while (data1.available()) {
               ch[count] = data1.read();
               count++;
   
          }
      }
   data1.close(); // Close the file
   char * buffer1;
   buffer1= (char*) malloc(70*sizeof(char));
   strcpy(buffer1, ch);
   fetchRadio(buffer1);
   free(buffer1);
 }
 }

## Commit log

2020-12-21 add BNO055 schematic and layout. Needs test points
    [BNO055_circuit_i2C.sch, BNO055_circuit_i2C_version_3.kicad_pcb]
2020-12-21 add MPL3115A2 schematic and layout. Needs test points
    [MPL3115A2_barometer.kicad_pcb, MPL3115A2_barometer.sch]
2020-12-29 add test point for CAP pin
    [MPL3115A2_barometer.kicad_pcb]
2020-12-29 add test points to schematic (not layout). Add power signs in lower-right of schematic
    [BNO055_circuit_i2C.sch, MPL3115A2_barometer.sch]
2020-12-29 SD and baro push test
    [barometer.kicad_pcb, barometer.sch, sd_card.kicad_pcb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]
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2020-12-29 Try hierarchical schematic - first pass
    [rev1.kicad_pcb, rev1.sch]
2020-12-29 Try hierarchical schematic - second pass
    [rev1.sch]
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2021-01-05 add level shifter to BNO055 schematic. Needs review
    [BNO055_circuit_i2C.sch]
2021-01-05 add level shifter to MLP3115A2. Needs review
    [BNO055_circuit_i2C.sch, MPL3115A2_barometer.sch]
2021-01-05 change net labels to global pin labels
    [BNO055_circuit_i2C.sch]
2021-01-05 Schematic: connect Teensy to BNO055 and MPL
    [rev1.sch]
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2021-01-06 Fix folder hierarchy issue
    [BMI088.kicad_pcb, BMI088.sch]
2021-01-07 Complete 1st revision schematic
    [revision1-Jan-11-20.kicad_pcb, revision1-Jan-11-20.sch]
2021-01-16 change BNO055 section of the rev1 schematic to use a two-pin crystal with capacitors
    [rev1.sch]
2021-01-16 fix annotation
    [rev1.sch]
2021-01-16 add abd change footprints
    [rev1.kicad_pcb, rev1.sch]
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2021-01-16 finish BNO055 portion of layout
    [rev1.kicad_pcb]
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2021-01-16 finish layout of BNO055, MPL3115A2, connected to Teensy. Change some pin choices on Teensy for easier connection.
    [rev1.kicad_pcb]
2021-01-19 (mostly) fix electrical rules check
    [rev1.kicad_pcb, rev1.sch]
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2021-01-19 spread components out, increase track size, rename test points, increase test point size
    [rev1.kicad_pcb]
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2021-01-19 add 2-pin header for BMS connection
    [rev1.kicad_pcb, rev1.sch]
2021-01-20 mirror all components by flipping and manually reversing sides. Fixes BNO055 and MPL3115 footprint mirroring. (All other components also reversed but symmetrical. Teensy not flipped.) Reassign pins o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
    [rev1.kicad_pcb, rev1.sch]
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2021-01-21 make GND zones cover entire PCB, front and back
    [rev1.kicad_pcb]
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2021-01-21 flip solder pads to match the same side as components
    [rev1.kicad_pcb]
2021-01-22 add BMI088 and ADXL345 to schematic. Import ADXL345 from SnapEDA into separate schematic
    [ADXL345.kicad_pcb, ADXL345.sch, rev1.sch]
2021-01-23 connect ADXL345 and BMI088 and GPS to Teensy in schematic
    [rev1.sch]
2021-01-23 add ADXL345 and BMI088 to layout
    [rev1.kicad_pcb, rev1.sch]
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2021-01-24 connect headers for GPS and radio to Teensy in schematic
    [rev1.sch]
2021-01-24 create symbol and footprint for RFM9X
    [rev1.sch]
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2021-01-25 add diode between Vin on Teensy and VDD on BMS
    [rev1.kicad_pcb, rev1.sch]
2021-01-25 add olin logo and design information
    [rev1.kicad_pcb]
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2021-01-25 modify circuit for power input from BMS on schematic
    [rev1.sch]
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2021-01-25 fix netlist, wip
    [rev1.kicad_pcb]
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2021-01-25 fix GPS power connection in layout
    [rev1.kicad_pcb]
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2021-02-06 copy Rev1 into Rev2. Change power input circuit from using MOSFET to TPS2113
    [BOM.csv, kicadbom.csv, rev1.sch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]
2021-03-26 Remove BNO055 and BMI055 from Rev2 schematic. Add 4.99K pull up resistors for SCL and SDA lines
    [rev1_I2C_test.kicad_pcb, rev1_I2C_test.sch, rev2.sch]
2021-03-26 fix some DRC errors
    [rev2.sch]
2021-03-27 change connector, power supply circuit, add buzzer
    [MainFlightComputer.dxf, PKB24SPCH3601-B0.step, rev2.sch]
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2021-04-02 add zener diode overvoltage protection, add 10 uF capacitor to radio, add LEDS but do not connect
    [rev2.sch]
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2021-04-07 Added data analysis code
    Added jupyter notebook that converts raw binary data into usable csv.
    [Flight_1.csv]
2021-04-07 Moved binary to csv into separate file.
    Added vscode and pyc files to gitignore.
    Moved binary to csv conversion into binary_to_csv.py.
    [Flight_1.csv]
2021-04-09 change size of buzzer
    [rev2.kicad_pcb]
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2021-04-12 Add exponential moving average and isApogee
    Adds a function for exponential moving average and isApogee.
    Exponential moving average puts in the unfiltered altitude with fewer
    than numValues values, which is currently set to 20. It puts in the SMA
    for the numValue value, and finds the EMA with a smoothing factor of 2
    after that. isApogee starts returns false before 5 seconds or if there
    are fewer than 20 points in the array. Since the array restarts after
    writing to the SD card every time, this means that there will be
    approximately 600 ms after each write that apogee will not be found.
    A design choice that must be made is how to deal with resetting the
    array every so often, resulting in the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
    [Rev1FlightComp.ino]
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2021-11-17 Added teensy footprint library and schematic for REV1 board (still needs pins connected)
    [REV1_FALL_2021.kicad_pcb, REV1_FALL_2021.sch, Teensy_4.0_Assembly.STEP]
2021-11-18 Mapped pins on teensy to pins on breakout chips
    [REV1_FALL_2021.sch]
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2021-11-18 Revert "add pinout image"
    This reverts commit 4e82854de17fd84ee4482139b0b4ce72b35bd257.
    [REV1_FALL_2021.sch]
2021-11-18 update libraries and resolve merge conflict
    [REV1_FALL_2021.sch]
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2021-11-18 Added outlines on the breakout board's footprints. Assembled PCB with wires, needs checking by Ian
    [REV1_FALL_2021.kicad_pcb, REV1_FALL_2021.sch]
2021-11-19 Verify pin connections on layout and fix mistakes
    [REV1_FALL_2021.kicad_pcb, REV1_FALL_2021.sch]
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2021-11-21 fix hierarchical sheet duplicates
    [REV1_FALL_2021.sch, TPS2113A_Teesny.sch]
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2021-11-25 add positive and negative signs on battery terminals
    [REV1_FALL_2021.kicad_pcb]
2021-11-25 add fab-outputs with BOM, CPL, and Gerber files (round 1)
    [BOM.csv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]
2021-11-25 Change footprint of TPS2113A to the TSSOP package
    [REV1_FALL_2021.kicad_pcb, REV1_FALL_2021.sch, TPS2113A_Teesny.sch]
2021-11-25 add dot to pin 1 of TPS2113A, rewire traces slightly
    [REV1_FALL_2021.kicad_pcb]
2021-11-25 add series resistor to improve accuracy of ILIM resistor
    It used to be a 400 ohm resistor, but those are not in stock in JLC's assembly parts. Now it is two 200 ohm resistors in series. It is important to get the values precise, because the maximum rating 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
    [REV1_FALL_2021.kicad_pcb, TPS2113A_Teesny.sch]
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2022-01-23 change both VSNS pins on multiplexers to use the same voltage divider
    [REV1_FALL_2021.sch]
2022-01-23 add additional solderable terminals to arming switches and ematch connections
    [REV1_FALL_2021.sch]
2022-01-23 add digital key switch connection to Teensy with pull-down resistor
    [REV1_FALL_2021.sch]
2022-01-25 create buzzer footprint
2022-01-25 add buzzer to Rev2 schematic and layout
    [REV1_FALL_2021.kicad_pcb, REV2_SPRING_2022.kicad_pcb, REV2_SPRING_2022.sch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]
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2022-01-26 remove hardware electrical arming (now using software arming)
    [REV2_SPRING_2022.kicad_pcb, REV2_SPRING_2022.sch]
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2022-01-29 move buzzer
    [REV2_SPRING_2022.kicad_pcb]
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2022-02-25 Still errors when compiling in the addDataPoint.ino file
    [Spring_2022_Main.ino, addDataPoint.ino, setupSensors.ino]
2022-03-01 fixed bug with addDataPoint
    [addDataPoint.ino]
2022-03-04 FIXED THE OFFLINE RADIO ISSUE
    [Base_Station_Radio.ino, On_Board_Radio.ino]
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2022-03-08 fixed sensor mapping
2022-03-09 Fixed functions to make phases work for testing
    [Flight_1.csv]
2022-03-09 fixed errors in compiling
    [Spring_2022_Main.ino, addDataPoint.ino, fetchAccelerometerData.ino]
2022-03-10 fixed a few bugs
    [Spring_2022_Main.ino, addDataPoint.ino]
2022-03-21 Added code for buzzer
    [On_Board_Radio.ino, Spring_2022_Main.ino, setupSensors.ino]
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2022-03-30 fixed kalman filter input from milliseconds to seconds.
    [addDataPoint.ino, kalman_update.cpp]
2022-04-16 added more to kalman testing + fixed kalman dt bug (needs to be added to main code)
    [4_15_22_test2.csv, 4_15_22_test3.csv, 4_15_22_test4.csv]
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2022-11-02 Change minor labeling error in teensy boards kicad
    [board_4.kicad_sch, board_one_teensy_22.kicad_sch]
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2022-11-09 Add ME2108, add power sys Schema v1, update readme
    Push to fork because write access on sensing wasn't working. Also, added readme
    [Avoinics Power System.kicad_pcb, Avoinics Power System.kicad_sch]
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

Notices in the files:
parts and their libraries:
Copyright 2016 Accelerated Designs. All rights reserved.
